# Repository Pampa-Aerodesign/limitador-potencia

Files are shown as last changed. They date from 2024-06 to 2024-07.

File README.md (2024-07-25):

# limitador-potencia
Sistema limitador de potência para motores BLDC com foco no Aerodesign.

# Objetivo
Estamos utilizando um limitador de potência a fim de cumprir as restrições do regulamento.
Nosso GMP (conjunto motor/hélice/bateria) é capaz de consumir mais de 800 W de potência, então,
para maximizar o empuxo e a pontuação na competição, desenvolvemos este sistema.

# Como funciona
O sistema é composto por dois Arduinos Nano executando o mesmo código.
Os dois Arduinos vão fazer a leitura dos sensores de corrente e de tensão,
do sinal PWM vindo do ESC.

Após realizar as leituras, cada Arduino vai calcular um novo PWM para o motor levando em conta
a potência obtida dos sensores, de modo que a potência do motor não ultrapasse um determinado valor.

Cada Arduino também faz a leitura do PWM gerado pelo outro e verifica se o valor está dentro
de uma tolerância. Caso um dos Arduinos perceba que o PWM do outro Arduino está fora da tolerância,
seja por uma discrepância nos valores ou por uma falha no segundo Arduino,
um pino de verificação (Check) será levado ao nível lógico baixo, fazendo com que o PWM
dos Arduinos seja barrado e o PWM do receptor seja enviado ao ESC.

# Estrutura do repositório
- **limitador-potencia.ino** - Arquivo principal que inicializa o sistema;
- **params.hpp** - Arquivo que contém todas as configurações do sistema. Nele, são definidos os pinos, parâmetros, estruturas de dados e constantes;
- Pasta **src/** - Arquivos fonte contendo as funções utilizadas no arquivo principal;
- Pasta **inc/** - Arquivos cabeçalho contendo os protótipos das funções.

### Arquivos fonte:
- **current.cpp** - funções relacionadas à leitura de corrente do motor;
- **voltage.cpp** - funções relacionadas à leitura de tensão da bateria;
- **pwm.cpp** - funções relacionadas à leitura dos sinais de PWM;

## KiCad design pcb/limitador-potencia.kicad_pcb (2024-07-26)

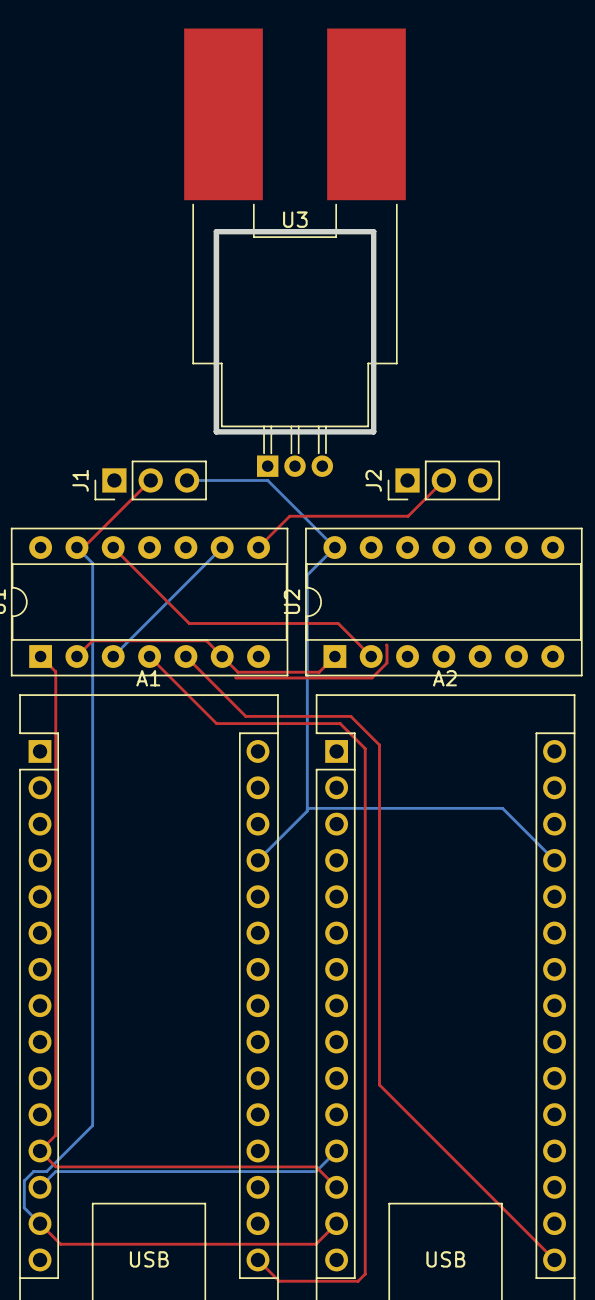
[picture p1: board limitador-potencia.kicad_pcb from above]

Board: 2 copper layers, 7 parts (0 on the bottom side), 14 nets.

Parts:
A1, A2: Arduino_Nano_v2.x; Arduino_Nano
J1: RX Input; PinHeader_1x03_P2.54mm_Vertical
J2: ESC Output; PinHeader_1x03_P2.54mm_Vertical
U1: 74HC00; CERDIP-14_W7.62mm_SideBrazed_Socket
U2: 74AHC04; CERDIP-14_W7.62mm_SideBrazed_Socket
U3: ACS758xCB-100B-PSF; Allegro_CB_PSF

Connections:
+5V: A1.27 (+5V), A2.27 (+5V), J1.3, U1.14 (VCC), U2.14 (VCC), U3.1 (VCC)
GND: A1.4 (GND), A1.29 (GND), A2.4 (GND), A2.29 (GND), J1.1, J2.1, U1.7 (GND), U2.7 (GND), U3.2 (GND)
unnamed: A1.19 (A0), A2.19 (A0), U3.3 (VIOUT)
unnamed: A1.24 (A5), A2.24 (A5)
unnamed: A1.12 (D9), A2.13 (D10), U1.1
unnamed: A1.13 (D10), A2.12 (D9)
unnamed: A1.14 (D11), A2.14 (D11), J1.2, U1.13
unnamed: A1.16 (D13), U1.4
unnamed: A2.16 (D13), U1.5
unnamed: J2.2, U1.8
unnamed: U1.2, U1.6, U2.1
unnamed: U1.3, U1.9
unnamed: U1.10, U1.11
unnamed: U1.12, U2.2

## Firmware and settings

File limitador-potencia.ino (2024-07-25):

#include <Servo.h>
#include <PID_v1.h>

#include "params.hpp"
#include "inc/pwm.hpp"
#include "inc/current.hpp"
#include "inc/voltage.hpp"

// Input PWM channels
Channels_t Channels[NUM_CHANNELS] = {0};

// Servo object (calculated PWM output for the ESC)
Servo esc;

// PID's variables
double setpoint;        // Desired value of Power
double input;           // Calculated power
double output;          // PID's output that will be used to set the PWM

// Initial PID's Parameters
double kp = 2.0, ki = 5.0, kd = 1.0;

// Creating the PID Object
PID pid(&input, &output, &setpoint, kp, ki, kd, DIRECT);


void setup(){
  // DEBUG
  // Serial.begin(115200);

  esc.attach(9);  // attaches the ESC on pin 9 to the servo object

  // setup check pins
  pinMode(pinCheck, OUTPUT);
  digitalWrite(pinCheck, HIGH);

  // setup channel pins
  for(int i = 0; i < NUM_CHANNELS; i++){
    Channels[i].pin = PinsPWM[i];
    pinMode(Channels[i].pin, INPUT_PULLUP);
    Channels[i].pinStateLast = digitalRead(Channels[i].pin);
    Channels[i].tStart = micros();
  }
  // Define the range of PID's outputs (1000 a 2000)
  pid.SetOutputLimits(1000, 2000);

  // Enables the PID controller 
  pid.SetMode(AUTOMATIC);
}

void loop(){
  // read all PWM channels
  readPWMChannels(Channels);

  // PWM signal coming from the other Arduino and from the RX
  uint16_t pwmArduino = Channels[0].tWidth;
  uint16_t pwmRX = Channels[1].tWidth;

  // calculate limited PWM
  // this is where we read voltage and current from the battery
  // and calculate a new PWM so that power (volts * amps)
  // doesn't exceed a specified value
  uint16_t outputPWM;

  // reading of current
  // due to the library this data needs to be a Double
  double current = readCurrent();

  // reading of voltage
  // due to the library this data needs to be a Double
  double voltage = readVoltage();

  // calculation of power: (current * voltage)
  // due to the library this data needs to be a Double
  double power = voltage * current;

  // run the PID calculation
  pid.Compute();

  // PID controller is used to generate a new PWM
  // uses a cast to guarantee 16-bit integer format
  outputPWM = static_cast<uint16_t>(output);

  // check if calculated PWM is close to the PWM calculated by the other arduino
  if(inRange(outputPWM, pwmArduino, TOLERANCE)){
    // PWM is within tolerance, output HIGH on the Check pin
    digitalWrite(pinCheck, HIGH);
  }
  else{
    // PWM is out of range, set check pin to low
    digitalWrite(pinCheck, LOW);
  }

  // send calculated PWM signal to the ESC
  esc.writeMicroseconds(outputPWM); 
}


// Return true if value is close to the reference plus or minus tolerance
bool inRange(uint16_t value, uint16_t reference, uint16_t tolerance){
  return (value <= reference+tolerance && value >= reference-tolerance);
}

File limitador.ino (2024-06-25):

#include <Servo.h>

// number of PWM inputs
#define NUM_CHANNELS 2

#define MAXPWM 2000

// Check pin input and output
const uint8_t pinCheckOut = 13;
const uint8_t pinCheckIn = 12;

// PWM input pins
const uint8_t pinPWMArduino = 10;
const uint8_t pinPWMRX = 11;

int maxFlag = 0;

const uint8_t pinsPWM[] = {
  pinPWMArduino,
  pinPWMRX
};

// Channel struct
typedef struct structChannels{
  uint8_t   pin;            // Channel pin
  uint8_t   pinStateLast;   // Last state the pin was in (HIGH or LOW)
  uint32_t  tStart;         // Time in microseconds the pin changed to HIGH
  uint32_t  tWidth;         // Width of the pulse in microseconds
} sChannels_t;

sChannels_t Channels[NUM_CHANNELS] = {0};

// Servo object (calculated PWM output for the ESC)
Servo esc;

void setup(){
  // Serial.begin(115200);

  esc.attach(9);  // attaches the ESC on pin 9 to the servo object

  // setup check pins
  pinMode(pinCheckOut, OUTPUT);
  pinMode(pinCheckIn, INPUT);
  digitalWrite(13, HIGH);

  // setup channel pins
  for(int i = 0; i < NUM_CHANNELS; i++){
    Channels[i].pin = pinsPWM[i];
    pinMode(Channels[i].pin, INPUT_PULLUP);
    Channels[i].pinStateLast = digitalRead(Channels[i].pin);
    Channels[i].tStart = micros();
  }
}

void loop(){
  // read PWM channels
  PWMRead();

  // calculate limited PWM
  // this is where we read voltage and current from the battery
  // and calculate a new PWM
  // so that power (volts * amps) doesn't exceed a specified value
  uint16_t pwm = 1200; // placeholder

  // generate calculated PWM servo signal
  esc.writeMicroseconds(pwm); 

  // PWM signal coming from the other Arduino and from the RX
  uint16_t pwmArduino = Channels[0].tWidth;
  uint16_t pwmRX = Channels[1].tWidth;

  // read check pin
  uint8_t check = digitalRead(pinCheckIn);

  // check if calculated PWM is close to the PWM calculated by the other arduino
  if(inRange(pwm, pwmArduino, 100)){
    // PWM is within range, output HIGH on the Check pin
    digitalWrite(pinCheckOut, HIGH);
  }
  else{
    // PWM is out of range, output negated Check pin from the other Arduino
    digitalWrite(pinCheckOut, !check);
  }
}

// Return true if value is close to the reference plus or minus tolerance
bool inRange(uint16_t value, uint16_t reference, uint16_t tolerance){
  return (value <= reference+tolerance && value >= reference-tolerance);
}

// This function will read all PWM channels
// and store the pulse width in microseconds
void PWMRead(){
  // Current channel
  static uint8_t channel = 0;

  // Current time in microseconds
  uint32_t timeNow = micros();

  // each pass we check one channel
  // read the state of the input
  uint8_t pinStateNow = digitalRead(Channels[channel].pin);

  if((timeNow - Channels[channel].tStart) > MAXPWM){
    Channels[channel].tWidth = 900;
    maxFlag = 1;
  }

  // if pin state changed (different than last)
  if(maxFlag == 0){
    if(pinStateNow != Channels[channel].pinStateLast){        
      // save as new last
      Channels[channel].pinStateLast = pinStateNow;

      if(pinStateNow == HIGH){            
        // pin changed from low to high; log the current time
        Channels[channel].tStart = timeNow;
      }
      else{
        // pin changed from high to low; current time minus start time is the pulse width
        Channels[channel].tWidth = timeNow - Channels[channel].tStart;

        // map tWidth to 0-180 (this function is not used so it was commented out)
        //Channels[channel].degrees = (uint8_t) map(Channels[channel].tWidth, 1100, 1900, 0, 180);

        // print channel PWM width
        // if(channel == 0 && millis()%500 < 20){
        //   Serial.print("\tCH:");     
        //   Serial.print(channel+1);
        //   Serial.print(" ");
        //   Serial.println(Channels[channel].tWidth);
        // }
      }
    }
  }

  if(pinStateNow == LOW){
    Channels[channel].pinStateLast = LOW;
    Channels[channel].tStart = timeNow;
    maxFlag = 0;
  }

  // go to next channel
  if(++channel >= NUM_CHANNELS)
    channel = 0;
}

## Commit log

2024-07-16 Renamed limitador.ino to limitador-potencia.ino Arduino requires the .ino file to have the same name as the parent folder Added .gitignore Moved things around to make more sense
2024-07-19 Inclusion of PID controller for generate a new PWM output using PID Library from Arduino Community
2024-07-25 Removed input check pin
2024-07-25 Voltage measurement implemented
    UNTESTED
2024-07-25 Current measurement implemented
    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
2024-07-26 Added KiCad schematic Schematic and PCB are not complete
    [limitador-potencia.kicad_pcb, limitador-potencia.kicad_sch]
